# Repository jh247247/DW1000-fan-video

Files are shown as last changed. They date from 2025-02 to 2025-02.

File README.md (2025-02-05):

# DW1000 fan pointing thingamagjig

This is the system shown off in [My video](https://youtu.be/dcd7I6KgY1Y) where I make an indoor location system to get a fan to point at me.

This uses the DW1000 UWB module to determine distances between radios in a 3d space, at minimum 4 fixed anchors.

This is very MVP software without power or feature optimizations, but it does work.

# Principle of operation

The DW1000 can determine distances between 2 radios using what is called Asymmetric Two Way Ranging. You can read about it here: https://www.qorvo.com/products/d/da008448

Using those distances, you can uniquely determine a point in 3d space that a radio exists in, given that space has at least 4 stationary radios spread out the area.

Since the measurements in this system are imperfect, the Levenberg-Marquandt algorithm is used to minimize the error in the measurements and find the best fitting point the tag could exist in.

Therefore, by finding the tag's position in 3d space you can have fun interations between them!

The application given in the linked video is trivial, but is an actual in-the-wild application of the technology outside of proof of concepts.
Future work that may or may not be added here:

- a CNC gantry to move a camera to a location given by another tag
- a gimbal for a spotlight to point at a subject
- "Hot zones" where emergency stops are enabled when a subject enters a known dangerous area
- ???

# Structure

Everything here can be considered MVP at best or broken at worst.

_hardware_
This is currently the broken version shown in the video, it has to be patched to get everything working. Hopefully I can get around to it.

- The power supply in power.sch is completely wrong - VCC is taken off the wrong side of the inductor
- MOSI is not attached to the DW1000
- RST is not attached to the DW1000 (optional - can have polling instead)
- IRQ is not attached to the DW1000 (optional - can have polling instead)
- The QMC5883L Compass is not working and doesn't respond to I2C commands - unknown as to why

# Installation

1. Have a home assistant instance up and running with an MQTT server and node-red
2. Add your secrets (WIFI SSID, Password, mqtt server, hopes and dreams) to secrets.cpp
3. Plug in your hardware into usb and run the esp32-s3 target (via platform.io) to run a skeleton sketch that prints out info
4. Note down the host name
5. Modify the platformio.ini file to add a target for your specific hardware. Add either `-DDW1000_ANCHOR` or `-DDW1000_TAG` to set that board as an anchor or tag. Examples from my hardware is provided.
6. Program your board ota using the new platform.io target you've added
7. Rinse and repeat for all your boards.
8. Import the `flows.json` file into your node red instance and duplicate the `Tag` subflow nodes. Add your mac address as it appears in the logs as the `TAG_MAC` env var for that subflow
9. Make sure you add the coordinates for the anchors, this is completely up to you. I recommend setting one as (0,0) with some height off the ground to reference off that one
10. The coordinates for your tags should start updating automatically and be available in Home Assistant for your automations
11. ???
12. Profit!

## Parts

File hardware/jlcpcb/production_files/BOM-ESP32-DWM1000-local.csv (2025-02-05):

Comment | Designator | Footprint | LCSC | Quantity
470R | R1,R10,R11,R15,R16,R2,R3,R4,R5,R6,R7,R8 | R_0603_1608Metric | C114669 | 12
LSM6DSLTR | U6 | LGA-14_L3.0-W2.5-P0.50-TL | C126672 | 1
AO3401A | Q3 | SOT-23 | C15127 | 1
100n | C1,C10,C11,C7 | C_0603_1608Metric | C1525 | 4
47u | C4,C5,C6 | CP_EIA-3216-10_Kemet-I | C16780 | 3
10u | C2,C3 | C_0805_2012Metric | C17024 | 2
S8050 | Q1,Q2 | SOT-23 | C181158 | 2
220n | C8 | C_0603_1608Metric | C21120 | 1
4.7k | R9 | R_0603_1608Metric | C23162 | 1
5.1k | R13,R14 | R_0603_1608Metric | C23186 | 2
100k | R12 | R_0603_1608Metric | C25803 | 1
TYPE-C 16PIN 2MD(073) | USB1 | USB-C-SMD_TYPE-C-6PIN-2MD-073 | C2765186 | 1
GT-TC070B-H016-L1 | SW1,SW2 | SW-SMD_4P-L4.6-W4.6-P3.00-LS6.1 | C2843954 | 2
MDA4020-2R2M | L1 | IND-SMD_L4.5-W4.1_YXMAA0402 | C2847469 | 1
ESP32-S3-WROOM-1(N16R8) | U2 | WIRELM-SMD_ESP32-S3-WROOM-1 | C2913202 | 1
SBR3M30P1-7 | D5 | POWERDI123_L2.8-W1.8-LS3.7-RD | C460953 | 1
Conn_02x10_Odd_Even | J1,J2 | PinHeader_2x10_P1.27mm_Vertical | C7470093 | 2
AP63203WU | U4 | TSOT-23-6 | C780769 | 1
DWM1000 | U1 | WIRELM-TH_DWM1000 | C95238 | 1
LED | D1,D2,D3,D4,D6,D7 | LED_0805_2012Metric | C965813 | 6
CP2102N-A02-GQFN24R | U3 | QFN-24_L4.0-W4.0-P0.50-TL-EP2.6 | C969151 | 1
QMC5883L | U5 | LGA-16_L3.0-W3.0-P0.50-BL_SQ | C976032 | 1
4.7u | C9 | C_0805_2012Metric | C98192 | 1

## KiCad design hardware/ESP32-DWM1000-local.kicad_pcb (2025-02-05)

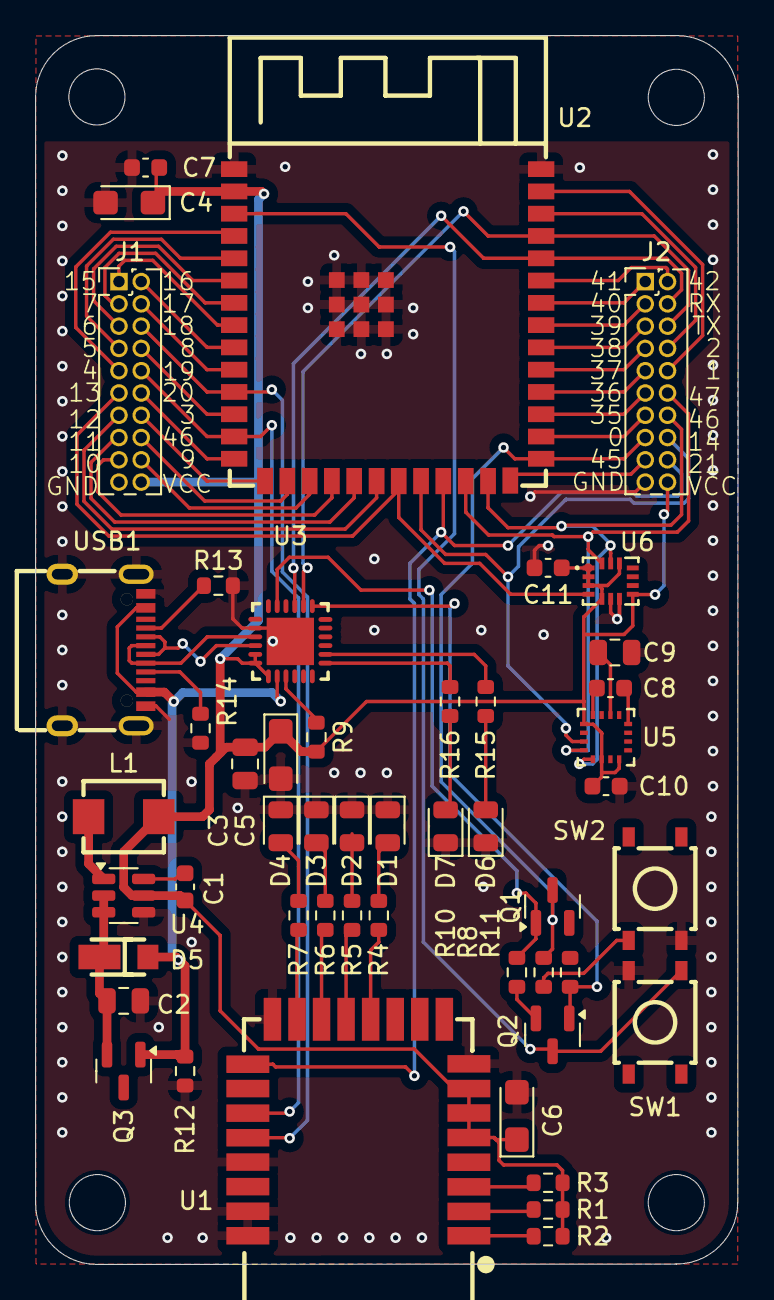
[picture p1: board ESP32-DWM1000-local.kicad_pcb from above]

Board: 2 copper layers, 40.1 x 70.1 mm, 53 parts (0 on the bottom side), 71 nets.

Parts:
C1, C7, C10, C11: 100n; C_0603_1608Metric
C2, C3: 10u; C_0805_2012Metric
C4, C5, C6: 47u; CP_EIA-3216-10_Kemet-I
C8: 220n; C_0603_1608Metric
C9: 4.7u; C_0805_2012Metric
D1, D2, D3, D4, D6, D7: LED; LED_0805_2012Metric
D5: SBR3M30P1-7; POWERDI123_L2.8-W1.8-LS3.7-RD
H1, H2, H3, H4: MountingHole; MountingHole_3.2mm_M3
J1, J2: Conn_02x10_Odd_Even; PinHeader_2x10_P1.27mm_Vertical
L1: MDA4020-2R2M; IND-SMD_L4.5-W4.1_YXMAA0402
Q1, Q2: S8050; SOT-23
Q3: AO3401A; SOT-23
R1, R2, R3, R4, R5, R6, R7, R8, R10, R11, R15, R16: 470R; R_0603_1608Metric
R9: 4.7k; R_0603_1608Metric
R12: 100k; R_0603_1608Metric
R13, R14: 5.1k; R_0603_1608Metric
SW1, SW2: GT-TC070B-H016-L1; SW-SMD_4P-L4.6-W4.6-P3.00-LS6.1
U1: DWM1000; WIRELM-TH_DWM1000
U2: ESP32-S3-WROOM-1(N16R8); WIRELM-SMD_ESP32-S3-WROOM-1
U3: CP2102N-A02-GQFN24R; QFN-24_L4.0-W4.0-P0.50-TL-EP2.6
U4: AP63203WU; TSOT-23-6
U5: QMC5883L; LGA-16_L3.0-W3.0-P0.50-BL_SQ
U6: LSM6DSLTR; LGA-14_L3.0-W2.5-P0.50-TL
USB1: TYPE-C 16PIN 2MD(073); USB-C-SMD_TYPE-C-6PIN-2MD-073

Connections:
CP2102_DM: U3.4 (D-), USB1.5 (DN2), USB1.7 (DN1)
CP2102_DP: U3.3 (D+), USB1.6 (DP1), USB1.8 (DP2)
CP2102_DTR: Q1.1 (E), R10.2, U3.23 (DTR)
CP2102_REGIN: C1.1, C3.1, C4.1, C5.1, C6.1, C7.1, C10.2, C11.2, J1.20, J2.20, L1.1, R1.1, R2.1, R3.1, R9.1, U1.5 (VDDAON), U1.6 (VDD3V3), U1.7 (VDD3V3), U2.2 (3V3), U3.5 (VIO), U3.6 (VDD), U3.7 (VREGIN), U4.5 (SW), U5.2 (VDD), U5.4 (S1), U5.13 (VDDIO), U6.1 (SDO/SA0), U6.2 (SDX), U6.3 (SCX), U6.5 (VDDIO), U6.8 (VDD), U6.12 (CS)
CP2102_RTS: Q2.1 (E), R11.2, U3.19 (RTS)
CP2102_RX: J2.6, U2.37 (TXD0), U3.20 (RXD)
CP2102_RXLED: R16.2, U3.13 (GPIO.1/RXT)
CP2102_TX: J2.4, U2.36 (RXD0), U3.21 (TXD)
CP2102_TXLED: R15.2, U3.14 (GPIO.0/TXT)
CP2102_VBUS: D5.1 (A), Q3.1 (G), R12.1, U3.8 (VBUS), USB1.2 (VBUS), USB1.11 (VBUS)
DWM_LEDRXOK: R7.2, U1.15 (GPIO0RXOKLED)
DWM_LEDTX: R4.2, U1.12 (GPIO3TXLED)
DWM_RXLED: R5.2, U1.13 (GPIO2RXLED)
DWM_SFDLED: R6.2, U1.14 (GPIO1SFDLED)
GND: C2.2, C3.2, C4.2, C5.2, C6.2, C7.2, C9.2, C10.1, C11.1, D1.1 (K), D2.1 (K), D3.1 (K), D4.1 (K), D6.1 (K), D7.1 (K), J1.19, J2.19, R12.2, R13.2, R14.2, SW1.3, SW2.3, U1.8 (VSS), U1.16 (VSS), U1.21 (VSS), U1.23 (VSS), U1.24 (VSS), U2.1 (GND), U2.40 (GND), U2.41 (GND), U3.2 (GND), U3.25 (GND), U4.4 (GND), U5.9 (GND), U5.11 (GND), U6.6 (GND), U6.7 (GND), USB1.1 (GND), USB1.12 (GND), USB1.13 (SHELL), USB1.14 (SHELL)
I2C_SCL: J2.14, U2.25 (IO48), U5.1 (SCL), U6.13 (SCL)
I2C_SDA: J2.12, U2.24 (IO47), U5.16 (SDA), U6.14 (SDA)
IO0: J2.15, Q1.3 (C), R8.1, U2.27 (IO0)
IO1: J2.10, U2.39 (IO1)
IO2: J2.8, U2.38 (IO2)
IO3: J1.14, U2.15 (IO3)
IO4: J1.9, U2.4 (IO4)
IO5: J1.7, U2.5 (IO5)
IO6: J1.5, U2.6 (IO6)
IO7: J1.3, U2.7 (IO7)
IO8: J1.8, U2.12 (IO8)
IO9: J1.18, U2.17 (IO9)
IO10: J1.17, U2.18 (IO10)
IO11: J1.15, U2.19 (IO11)
IO12: J1.13, U2.20 (IO12)
IO13: J1.11, U2.21 (IO13), U6.4 (INT1)
IO14: J2.16, U2.22 (IO14), U5.15 (DRDY)
IO15: J1.1, U2.8 (IO15)
IO16: J1.2, U2.9 (IO16)
IO17: J1.4, U2.10 (IO17)
IO18: J1.6, U1.20 (SPICLK), U2.11 (IO18)
IO19: J1.10, U1.19 (SPIMISO), U2.13 (IO19)
IO20: J1.12, U2.14 (IO20)
IO21: J2.18, U1.17 (SPICSn), U2.23 (IO21)
IO35: J2.13, U2.28 (IO35)
IO36: J2.11, U2.29 (IO36)
IO37: J2.9, U2.30 (IO37)
IO38: J2.7, U2.31 (IO38)
IO39: J2.5, U2.32 (IO39)
IO40: J2.3, U2.33 (IO40)
IO41: J2.1, U2.34 (IO41)
IO42: J2.2, U2.35 (IO42)
IO45: J2.17, U2.26 (IO45)
IO46: J1.16, U2.16 (IO46)
unnamed: D1.2 (A), R4.1
unnamed: D2.2 (A), R5.1
unnamed: D3.2 (A), R6.1
unnamed: D4.2 (A), R7.1
unnamed: C2.1, D5.2 (K), Q3.2 (S), U4.2 (EN), U4.3 (IN)
unnamed: D6.2 (A), R15.1
unnamed: D7.2 (A), R16.1
unnamed: Q1.2 (B), R11.1
unnamed: Q2.2 (B), R10.1
unnamed: R8.2, SW2.1
unnamed: R2.2, U1.1 (EXTON)
unnamed: R3.2, U1.3 (RSTn)
unnamed: R1.2, U1.2 (WAKEUP)
unnamed: R9.2, U3.9 (RSTb)
unnamed: C1.2, U4.6 (BST)
unnamed: L1.2, U4.1 (FB)
unnamed: C9.1, U5.10 (C1)
unnamed: C8.2, U5.12 (SETC)
unnamed: C8.1, U5.8 (SETP)
unnamed: R13.1, USB1.4 (CC1)
unnamed: R14.1, USB1.9 (SBU1)
RESET: Q2.3 (C), SW1.1, U2.3 (EN)

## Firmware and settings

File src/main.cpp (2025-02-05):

#include <Arduino.h>
#include <QMC5883LCompass.h>
#include <Adafruit_LSM6DSL.h>
#include <DW1000Ng.hpp>
#include <DW1000NgUtils.hpp>
#include <DW1000NgTime.hpp>
#include <DW1000NgConstants.hpp>
#include <DW1000NgRanging.hpp>
#include <DW1000NgRTLS.hpp>

#include "dw1000.hpp"
#include "network.hpp"
#include <WiFi.h>
#include <esp_wifi.h>
#include "homeassistant.hpp"
#include <TMCStepper.h>
#include <Preferences.h>


#ifdef MOTOR_TMC2209
#include "motor.hpp"
#define STEPS_PER_REV 10000 // todo calibrate
#define STEP_PIN 7
#define DIR_PIN 6
Motor* stepper = new Motor(STEP_PIN, DIR_PIN, STEPS_PER_REV);

void interrupt() {
    stepper->motorInterrupt();
} 
#endif

Preferences* preferences;
QMC5883LCompass compass;
Adafruit_LSM6DSL lsm6dsl;
Adafruit_Sensor *lsm_temp, *lsm_accel, *lsm_gyro;
Network network;
DW1000* dw1000;
HomeAssistant* homeAssistant;



boolean compassWorking = false;
boolean accelWorking = false;


#define DWM1000_TAG 0
#define DWM1000_ANCHOR 1
#define DWM1000_MODE DWM1000_ANCHOR

volatile uint32_t blink_rate = 200;

const uint8_t DWM1000_RST = 9; // need to bodge this in hardware - forgot to connect
const uint8_t DWM1000_IRQ = 3; 
const uint8_t DWM1000_CS = 21;




void setup() {
    Serial.begin(921600);
    // set a pin high for testing
    pinMode(14, INPUT); // QMC5883L data ready pin
    Serial.println("Hello World!");

    preferences = new Preferences();
    preferences->begin("dw1000", false);

  #ifdef MOTOR_TMC2209
  
        // register timer interrupt for motor
    hw_timer_t *timer = NULL;
    timer = timerBegin(0, 80, true);
    timerAttachInterrupt(timer, interrupt, true);
    timerAlarmWrite(timer, 1000, true);
    timerAlarmEnable(timer);
    
  #endif
    

    network.connect();


    Wire.begin(47,48);

    byte error;

    // compass should live at 0x0D
    // need to test because at least one module is broken
    Wire.beginTransmission(0x0D);
    error = Wire.endTransmission();
    if (error == 0) {
        Serial.println("QMC5883L found at 0x0D");
        compassWorking = true;
        compass.init();
    } else {
        Serial.println("Compass 5883L not found at 0x0D - is it broken?");
    }

    // accel should live at 0x68
    Wire.beginTransmission(0x6B);
    error = Wire.endTransmission();
    if (error == 0) {
        Serial.println("LSM6DSLTR found at 0x6B");
        accelWorking = true;
        
        lsm6dsl.begin_I2C(0x6B, &Wire);
        lsm_temp = lsm6dsl.getTemperatureSensor();
        lsm_accel = lsm6dsl.getAccelerometerSensor();
        lsm_gyro = lsm6dsl.getGyroSensor();
    } else {
        Serial.println("LSM6DSLTR not found at 0x6B - is it broken?");
    }

    Serial.println("Initializing SPI...");
    pinMode(DWM1000_CS, OUTPUT);

    SPI.begin(18, 19, 20);

    Serial.println("SPI initialized");

    uint8_t macAddr[6];
    esp_wifi_get_mac(WIFI_IF_STA, macAddr);
    
    dw1000 = new DW1000(preferences, DWM1000_CS, DWM1000_IRQ, DWM1000_RST, macAddr);

#if defined(DW1000_ANCHOR) || defined(DW1000_TAG)
#ifdef MOTOR_TMC2209
    homeAssistant = new HomeAssistant(preferences, dw1000, stepper);
    #else
    homeAssistant = new HomeAssistant(preferences, dw1000);
    #endif
    
    homeAssistant->connect();
    
#endif
}

void loop() {
  network.handle();
  
// if anchor or tag run actual program
#if defined(DW1000_ANCHOR) || defined(DW1000_TAG)
  dw1000->handle();
  homeAssistant->handle();
#endif

#ifdef MOTOR_TMC2209
  // rotate 1 degree
  //stepper->step();
  // toggle step pin
  digitalWrite(STEP_PIN, !digitalRead(STEP_PIN));
#endif

  
  /*if(compassWorking) {
    compass.read();
    Serial.print("X: ");
    Serial.print(compass.getX());
    Serial.print(" Y: ");
    Serial.print(compass.getY());
    Serial.print(" Z: ");
    Serial.println(compass.getZ());
  }*/

  /*if(accelWorking) {
    sensors_event_t accel_event;
    lsm_accel->getEvent(&accel_event);
    Serial.println();
    Serial.println("Accelerometer information follows:");
    Serial.print("X: ");
    Serial.print(accel_event.acceleration.x);
    Serial.print(" Y: ");
    Serial.print(accel_event.acceleration.y);
    Serial.print(" Z: ");
    Serial.println(accel_event.acceleration.z);
  }*/
}

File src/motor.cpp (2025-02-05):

#include "motor.hpp"
#include <Arduino.h>
#include "network.hpp"

Motor::Motor(uint8_t stepPin, uint8_t dirPin, uint32_t stepsPerRev) {
    mStepPin = stepPin;
    mDirPin = dirPin;
    mStepsPerRev = stepsPerRev;
    mCurrentPosition = 0;
    mStepsRemaining = 0;
    mInitialized = false;
    pinMode(stepPin, OUTPUT);
    pinMode(dirPin, OUTPUT);
}

void Motor::motorInterrupt() {
    boolean currentStepPin = digitalRead(mStepPin);
    boolean currentDirPin = digitalRead(mDirPin);
    if(mStepsRemaining != 0) {
        pinMode(mStepPin, OUTPUT);
        digitalWrite(mStepPin, !currentStepPin);
        if(currentStepPin) {
            // we've completed a step
            int inc = currentDirPin ? -1 : 1;
            if(mCurrentPosition == 0 && inc == -1) {
                mCurrentPosition = mStepsPerRev;
            } else if(mCurrentPosition == mStepsPerRev && inc == 1) {
                mCurrentPosition = 0;
            }
            mCurrentPosition += inc;
            
            mStepsRemaining += currentDirPin ? 1 : -1;
        }
    } else {
        // set to input to prevent glitching
        pinMode(mStepPin, INPUT);
    }
    
}

void Motor::update(int angle) {
    if(mInitialized == false) {
        mInitialized = true;

        // first angle set, use this as the current position
        mCurrentPosition = angle * mStepsPerRev / 360;
        mStepsRemaining = 0;
        return;
    }    

    int targetPosition = angle * mStepsPerRev / 360;
    int distance = targetPosition - (mCurrentPosition + mStepsRemaining);
    int clockwiseDistance = (distance + mStepsPerRev) % mStepsPerRev;
    int counterClockwiseDistance = abs((int)((mStepsPerRev - clockwiseDistance) % mStepsPerRev));

    debugV("motor Clockwise distance: %d, Counter clockwise distance: %d", clockwiseDistance, counterClockwiseDistance);

    if(clockwiseDistance < counterClockwiseDistance) {
        mStepsRemaining += clockwiseDistance;
    } else {
        mStepsRemaining -= counterClockwiseDistance;
    }

    if(mStepsRemaining > 0) {
        digitalWrite(mDirPin, LOW);
    } else {
        digitalWrite(mDirPin, HIGH);
    }

    debugV("Updating motor to angle %d, current position %d, steps remaining: %d", angle, mCurrentPosition, mStepsRemaining);
}
